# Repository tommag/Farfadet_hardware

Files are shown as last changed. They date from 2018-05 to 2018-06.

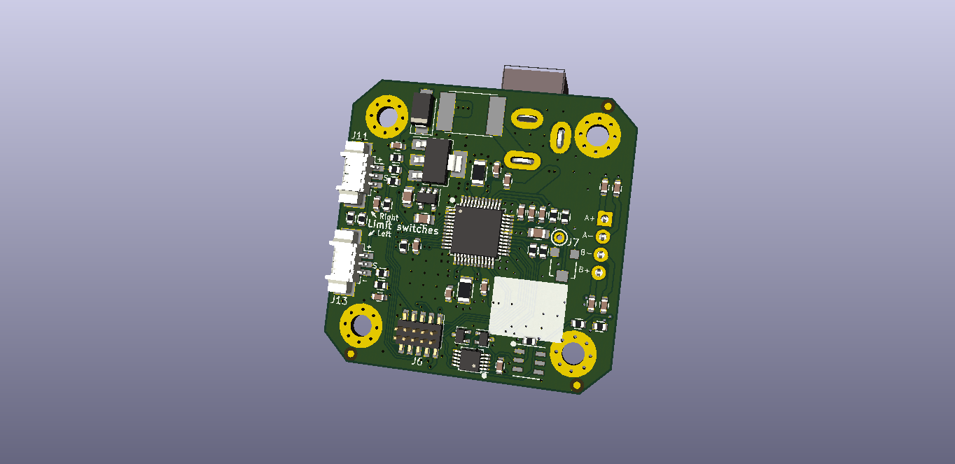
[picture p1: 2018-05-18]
Farfadet_stepper_driver_TMC5130/production/Farfadet_stepper_driver_TMC5130_3D_back.png

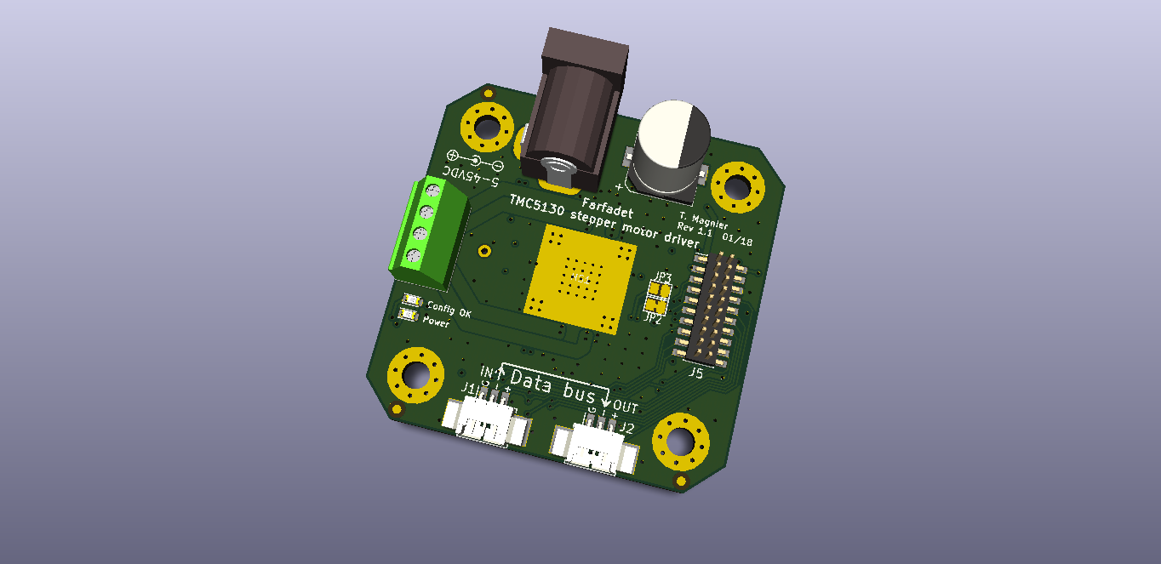
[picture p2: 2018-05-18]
Farfadet_stepper_driver_TMC5130/production/Farfadet_stepper_driver_TMC5130_3D_front.png

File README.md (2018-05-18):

# Farfadet Hardware

This repo contains KiCad EDA files for the Farfadet modular motor system.

You can check some info on the project here : <https://hackaday.io/project/45995-farfadet>

Each folder here contains a different hardware project. There is a schematic export in PDF format for each project. You can find the gerber files in the `gerber` directories. The Bill of Materials and component placement files are in the `production` directories. 

## License
This project is Open Source Hardware, licensed under the Creative Commons BY-SA 4.0 license. You can find the full license text here : <https://creativecommons.org/licenses/by-sa/4.0/>

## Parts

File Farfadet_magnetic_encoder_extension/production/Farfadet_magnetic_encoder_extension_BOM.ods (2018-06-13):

Farfadet – Magnetic encoder extension
Tom Magnier – v1.1 – 06/2018
Reference | Quantity | Value | Package | Digikey part # | Digikey unit price (EUR, qty 10) | Digikey total price
C1,C2 | 2 | 0.1uF | C_0603 | 445-5666-1-ND (https://www.digikey.fr/product-detail/fr/tdk-corporation/CGA3E2X7R1H104K080AA/445-5666-1-ND/2443706) | 0,026 | 0,052
D1 | 1 | Red | LED_0603 | 475-2512-1-ND (https://www.digikey.fr/product-detail/fr/osram-opto-semiconductors-inc/LS-Q976-NR-1/475-2512-1-ND/1802639) | 0,212 | 0,212
D2 | 1 | Green | LED_0603 | 511-1578-1-ND (https://www.digikey.fr/product-detail/fr/rohm-semiconductor/SML-D12M8WT86/511-1578-1-ND/1641810) | 0,21 | 0,21
J1 | 1 | Conn_02x05_Odd_Even | Socket_Strip_Straight_2x05_Pitch1.27mm_SMD | 609-3706-1-ND (https://www.digikey.fr/product-detail/fr/amphenol-fci/20021321-00010C4LF/609-3706-1-ND/2209151) | 0,706 | 0,706
R1 | 1 | 10k | R_0603 | 311-10KGRCT-ND (https://www.digikey.fr/product-detail/fr/yageo/RC0603JR-0710KL/311-10KGRCT-ND/729647) | 0,009 | 0,009
RN1,RN2 | 2 | 4*4.7k | R_Array_Convex_4x0603 | Y9472CT-ND (https://www.digikey.fr/product-detail/fr/panasonic-electronic-components/EXB-38V472JV/Y9472CT-ND/256600) | 0,09 | 0,18
U1 | 1 | AS5132-HSS* | SSOP-20_5.3x7.2mm_Pitch0.65mm | AS5132-HSSMCT-ND (https://www.digikey.fr/product-detail/fr/ams/AS5132-HSSM/AS5132-HSSMCT-ND/3586463) | 5,587 | 5,587
- | 1 | Magnet | NdFeB, Diametrical, diam. 6mm | 469-1024-ND (https://www.digikey.fr/product-detail/fr/radial-magnet-inc/8995/469-1024-ND/5126077) | 0,27 | 0,27
TOTAL |  |  |  |  |  | 7,226
 |  | Adhesive PCB standoff | Height : 6.4mm | RPC1096-ND (https://www.digikey.fr/product-detail/fr/essentra-components/LCBSBM-4-01A-RT/RPC1096-ND/392194) | 0,72

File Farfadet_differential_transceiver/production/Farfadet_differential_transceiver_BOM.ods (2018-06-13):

Farfadet – Differential transceiver for MCU
Tom Magnier – Rev1.0 – 01/2018
Reference | Qty 3.3V | Qty 5V | Value | Package | Digikey part # | Digikey unit price (EUR, qty 10) | Digikey total price | Farnell part # | Farnell unit price
C2 | 1 | 1 | 0.1uF | C_0603 | 445-5666-1-ND (https://www.digikey.fr/product-detail/fr/tdk-corporation/CGA3E2X7R1H104K080AA/445-5666-1-ND/2443706) | 0,026 | 0,026
C1,C3 |  | 2 | 0.1uF | C_0603 | 445-5666-1-ND (https://www.digikey.fr/product-detail/fr/tdk-corporation/CGA3E2X7R1H104K080AA/445-5666-1-ND/2443706) | 0,026 | 0,052
J1,J2 | 2 | 2 | Conn_01x05 | Pin_Header_Straight_1x05_Pitch2.54mm |  |  | 0
J3 | 1 | 1 | XLR connector | Neutrik_XLR_NC3FAAH2 |  |  | 0 | 1310023 (http://fr.farnell.com/neutrik/nc3faah2/socket-xlr-pcb-horizontal-3pole/dp/1310023?st=nc3faa) | 1,15
J4 | 1 | 1 | picoBlade connector | Molex_PicoBlade_53047-0310_03x1.25mm_Straight | WM1732-ND (https://www.digikey.fr/product-detail/fr/molex-llc/0530470310/WM1732-ND/242854) | 0,35 | 0,35
Q1 |  | 1 | BSS84 | SOT-23 | BSS84-FDICT-ND (https://www.digikey.fr/product-detail/fr/diodes-incorporated/BSS84-7-F/BSS84-FDICT-ND/717844) | 0,23 | 0,23
R1 | 1 | 1 | 1k | R_0603 | 311-1.0KGRCT-ND (https://www.digikey.fr/product-detail/fr/yageo/RC0603JR-071KL/311-1.0KGRCT-ND/729624) | 0,009 | 0,009
R3,R4 |  | 2 | 1k | R_0603 | 311-1.0KGRCT-ND (https://www.digikey.fr/product-detail/fr/yageo/RC0603JR-071KL/311-1.0KGRCT-ND/729624) | 0,009 | 0,018
R2 | 1 | 1 | 120R | R_0603 | 311-120GRCT-ND (https://www.digikey.fr/product-detail/fr/yageo/RC0603JR-07120RL/311-120GRCT-ND/729653) | 0,009 | 0,009
U1 |  | 1 | TXS0101DBV | SOT-23-6 | 296-22863-1-ND (https://www.digikey.fr/product-detail/fr/texas-instruments/TXS0101DBVR/296-22863-1-ND/1740010) | 0,54 | 0,54
U2 | 1 |  | SP3485CN | SOIC-8_3.9x4.9mm_Pitch1.27mm | ISL83485IBZ-ND (https://www.digikey.fr/product-detail/fr/intersil/ISL83485IBZ/ISL83485IBZ-ND/821562) | 1,109 | 1,109
U2 |  | 1 | ST485CDR | SOIC-8_3.9x4.9mm_Pitch1.27mm | 497-3734-1-ND (https://www.digikey.fr/product-detail/fr/stmicroelectronics/ST485CDR/497-3734-1-ND/686452) | 0,623 | 0,623
TOTAL |  |  |  |  |  |  | 2,966
 |  |  |  | picoBlade right angle | WM1743-ND (https://www.digikey.fr/product-detail/fr/molex-llc/0530480310/WM1743-ND/242865) | 0,38

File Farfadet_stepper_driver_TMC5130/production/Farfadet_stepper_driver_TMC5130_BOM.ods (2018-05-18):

Farfadet – TMC5130 stepper motor driver
Tom Magnier – Rev1.1 – 01/2018
Reference | Quantity | Value | Package | Digikey part # | Digikey unit price (EUR, qty 10) | Digikey total price
C1 | 1 | 220uF, 50V | CP_Elec_8x10.5 | PCE5025CT-ND (https://www.digikey.fr/product-detail/fr/panasonic-electronic-components/EEE-FT1H221AP/PCE5025CT-ND/2652080) | 0,593 | 0,593
C17,C22 | 2 | DNP | C_0603
C18,C19,C20,C21 | 4 | 470pF, 100V | C_0603 | 490-4949-1-ND (https://www.digikey.fr/product-detail/fr/murata-electronics-north-america/GCM1885C2A471JA16D/490-4949-1-ND/1765268) | 0,064 | 0,256
C2,C4,C5,C10,C15,C16 | 6 | 0.1uF, 16V | C_0603 | 445-5666-1-ND (https://www.digikey.fr/product-detail/fr/tdk-corporation/CGA3E2X7R1H104K080AA/445-5666-1-ND/2443706) | 0,026 | 0,156
C3,C11,C14 | 3 | 0.1uF, 50V | C_0603 | 445-5666-1-ND (https://www.digikey.fr/product-detail/fr/tdk-corporation/CGA3E2X7R1H104K080AA/445-5666-1-ND/2443706) | 0,026 | 0,078
C6 | 1 | 10uF, 10V | C_0805 | 1276-6456-1-ND (https://www.digikey.fr/product-detail/fr/samsung-electro-mechanics-america-inc/CL21A106KPFNNNG/1276-6456-1-ND/5958084) | 0,068 | 0,068
C7,C8 | 2 | 4.7uF, 10V | C_0805 | 1276-6500-1-ND (https://www.digikey.fr/product-detail/fr/samsung-electro-mechanics-america-inc/CL21F475ZPFNNNG/1276-6500-1-ND/5958128) | 0,06 | 0,12
C9 | 1 | 22nF, 63V | C_0603 | 399-3476-1-ND (https://www.digikey.fr/product-detail/fr/kemet/C0603C223K1RACTU/399-3476-1-ND/754769) | 0,028 | 0,028
D1 | 1 | 2A, 50V | D_SMA | B250A-FDICT-ND (https://www.digikey.fr/product-detail/fr/diodes-incorporated/B250A-13-F/B250A-FDICT-ND/768810) | 0,312 | 0,312
D2,D3 | 2 | D5V0L2B3W | SOT-323_SC-70 | D5V0L2B3W-7DICT-ND (https://www.digikey.fr/product-detail/fr/diodes-incorporated/D5V0L2B3W-7/D5V0L2B3W-7DICT-ND/2918820) | 0,226 | 0,452
D6 | 1 | Green | LED_0603 | 511-1578-1-ND (https://www.digikey.fr/product-detail/fr/rohm-semiconductor/SML-D12M8WT86/511-1578-1-ND/1641810) | 0,21 | 0,21
D7 | 1 | Red | LED_0603 | 475-2512-1-ND (https://www.digikey.fr/product-detail/fr/osram-opto-semiconductors-inc/LS-Q976-NR-1/475-2512-1-ND/1802639) | 0,212 | 0,212
F1 | 1 | 1.1A, 60V | Fuse_SMD2920 | F8134CT-ND (https://www.digikey.fr/product-detail/fr/littelfuse-inc/2920L110-60MR/F8134CT-ND/6234828) | 0,614 | 0,614
HS1 | 1 | Heatsink | Heatsink_Adhesive_10x10mm | AE10837-ND (https://www.digikey.fr/product-detail/fr/assmann-wsw-components/V2017B/AE10837-ND/3511410) | 0,48 | 0,48
J11,J2,J1,J13 | 4 | Conn_01x03 | Molex_PicoBlade_53261-0371_03x1.25mm_Angled | WM7621CT-ND (https://www.digikey.fr/product-detail/fr/molex-llc/0532610371/WM7621CT-ND/699108) | 0,84 | 3,36
J12 | 1 | Conn_01x04 | TerminalBlock_Pheonix_MPT-2.54mm_4pol | ED10563-ND (https://www.digikey.fr/product-detail/fr/on-shore-technology-inc/OSTVN04A150/ED10563-ND/1588864) | 1,17 | 1,17
J3 | 1 | BARREL_JACK | JACK_ALIM | CP-202A-ND (https://www.digikey.fr/product-detail/fr/cui-inc/PJ-202A/CP-202A-ND/252007) | 0,473 | 0,473
J5 | 1 | Conn_02x10_Odd_Even | Pin_Header_Straight_2x10_Pitch1.27mm_SMD |  |  | 0
J6 | 1 | Conn_02x05_Odd_Even | Pin_Header_Straight_2x05_Pitch1.27mm_SMD | 609-3695-1-ND (https://www.digikey.fr/product-detail/fr/amphenol-fci/20021121-00010C4LF/609-3695-1-ND/2209147) | 0,588 | 0,588
R11,R17 | 2 | DNP | R_0603 |  |  | 0
R12,R14 | 2 | 4.7k | R_0603 | 311-4.7KGRCT-ND (https://www.digikey.fr/product-detail/fr/yageo/RC0603JR-074K7L/311-4.7KGRCT-ND/729732) | 0,009 | 0,018
R2 | 1 | 10R | R_0603 | 311-10GRCT-ND (https://www.digikey.fr/product-detail/fr/yageo/RC0603JR-0710RL/311-10GRCT-ND/729646) | 0,009 | 0,009
R3 | 1 | 2.2k | R_0603 | 311-2.2KGRCT-ND (https://www.digikey.fr/product-detail/fr/yageo/RC0603JR-072K2L/311-2.2KGRCT-ND/729676) | 0,009 | 0,009
R4,R5 | 2 | 0R12 0.5W | R_1206 | 311-.12LYCT-ND (https://www.digikey.fr/product-detail/fr/yageo/RL1206FR-7W0R12L/311-.12LYCT-ND/3886125) | 0,285 | 0,57
R6,R1,R9,R15,R7,R18 | 6 | 10k | R_0603 | 311-10KGRCT-ND (https://www.digikey.fr/product-detail/fr/yageo/RC0603JR-0710KL/311-10KGRCT-ND/729647) | 0,009 | 0,054
R8,R10,R13,R16 | 4 | 0R | R_0603 | 311-0.0GRCT-ND (https://www.digikey.fr/product-detail/fr/yageo/RC0603JR-070RL/311-0.0GRCT-ND/729622) | 0,008 | 0,032
RV1 | 1 | 10k | Potentiometer_Trimmer-EVM3E | TC33X-103ECT-ND (https://www.digikey.fr/product-detail/fr/bourns-inc/TC33X-2-103E/TC33X-103ECT-ND/612911) | 0,235 | 0,235
U1 | 1 | TS3A24159DGSR | TSSOP-10_3x3mm_Pitch0.5mm | 296-21913-1-ND (https://www.digikey.fr/product-detail/fr/texas-instruments/TS3A24159DGSR/296-21913-1-ND/1629266) | 0,812 | 0,812
U2 | 1 | NCV4264-2ST50 | SOT-223-3Lead_TabPin2 | NCV4264-2ST50T3GOSCT-ND (https://www.digikey.fr/product-detail/fr/on-semiconductor/NCV4264-2ST50T3G/NCV4264-2ST50T3GOSCT-ND/2121724) | 0,879 | 0,879
U3 | 1 | MIC5365-3.3YD5 | SOT-23-5 | 576-4085-1-ND (https://www.digikey.fr/product-detail/fr/microchip-technology/MIC5365-3.3YD5-TR/576-4085-1-ND/3671753) | 0,14 | 0,14
U4 | 1 | DS2431P+T | TSOC-6_4x3.8mm_Pitch1.27mm | DS2431P+T&RCT-ND (https://www.digikey.fr/product-detail/fr/maxim-integrated/DS2431P-T-R/DS2431P-T-RCT-ND/3647900) | 1,383 | 1,383
U5 | 1 | TMC5130A | TQFP-48-1EP_7x7mm_Pitch0.5mm | 1460-1124-ND (https://www.digikey.fr/product-detail/fr/trinamic-motion-control-gmbh/TMC5130A-TA/1460-1124-ND/5030141) | 4,878 | 4,878
TOTAL |  |  |  |  |  | 18,189

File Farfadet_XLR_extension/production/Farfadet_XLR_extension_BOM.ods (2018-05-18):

Farfadet – XLR extension
Tom Magnier – Rev1.0 – 01/2018
Reference | Quantity | Value | Package | Digikey part # | Digikey unit price (EUR, qty 10) | Digikey total price | Farnell part # | Farnell unit price
C1 | 1 | 0.1uF, 50V | C_0603 | 445-5666-1-ND (https://www.digikey.fr/product-detail/fr/tdk-corporation/CGA3E2X7R1H104K080AA/445-5666-1-ND/2443706) | 0,026 | 0,026
C2 | 1 | 22uF, 25V | CP_Elec_6.3x4.5 | PCE3899CT-ND (https://www.digikey.fr/product-detail/fr/panasonic-electronic-components/EEE-1EA220SP/PCE3899CT-ND/766275) | 0,187 | 0,187
C3 | 1 | 1uF, 50V | C_0805 | 1276-3010-1-ND (https://www.digikey.fr/product-detail/fr/samsung-electro-mechanics/CL21F105ZBFNNNE/1276-3010-1-ND/3891096) | 0,069 | 0,069
J1 | 1 | XLR NC3MAAH | Neutrik_XLR_NC3MAAH |  |  | 0 | 1310044 (http://fr.farnell.com/neutrik/nc3maah/plug-xlr-pcb-horizontal-3pole/dp/1310044?st=nc3maa) | 1,08
J2 | 1 | Conn_02x10_Odd_Even | Socket_Strip_Straight_2x10_Pitch1.27mm_SMD | 609-3709-1-ND (https://www.digikey.fr/product-detail/fr/amphenol-fci/20021321-00020C4LF/609-3709-1-ND/2209161) | 1,357 | 1,357
J3 | 1 | XLR NC3FAAH2 | Neutrik_XLR_NC3FAAH2 |  |  | 0 | 1310023 (http://fr.farnell.com/neutrik/nc3faah2/socket-xlr-pcb-horizontal-3pole/dp/1310023?st=nc3faa) | 1,15
J4 | 1 | Conn_01x02 | TerminalBlock_Pheonix_MPT-2.54mm_2pol |  |  | 0
J5 | 1 | Conn_01x02 | JST_PH_B2B-PH-K_02x2.00mm_Straight | 455-1704-ND (https://www.digikey.fr/product-detail/fr/jst-sales-america-inc/B2B-PH-K-S-LF-SN/455-1704-ND/926611) | 0,14 | 0,14
R1 | 1 | 2.2k | R_0603 | 311-2.2KGRCT-ND (https://www.digikey.fr/product-detail/fr/yageo/RC0603JR-072K2L/311-2.2KGRCT-ND/729676) | 0,009 | 0,009
RV1 | 1 | 10k | Potentiometer_Trimmer-EVM3E | TC33X-103ECT-ND (https://www.digikey.fr/product-detail/fr/bourns-inc/TC33X-2-103E/TC33X-103ECT-ND/612911) | 0,235 | 0,235
U1 | 1 | NCV4276BDTADJRKG | TO-252-4 | NCV4276BDTADJRKGOSCT-ND (https://www.digikey.fr/product-detail/fr/on-semiconductor/NCV4276BDTADJRKG/NCV4276BDTADJRKGOSCT-ND/3487445) | 1,231 | 1,231
TOTAL |  |  |  |  |  | 3,254

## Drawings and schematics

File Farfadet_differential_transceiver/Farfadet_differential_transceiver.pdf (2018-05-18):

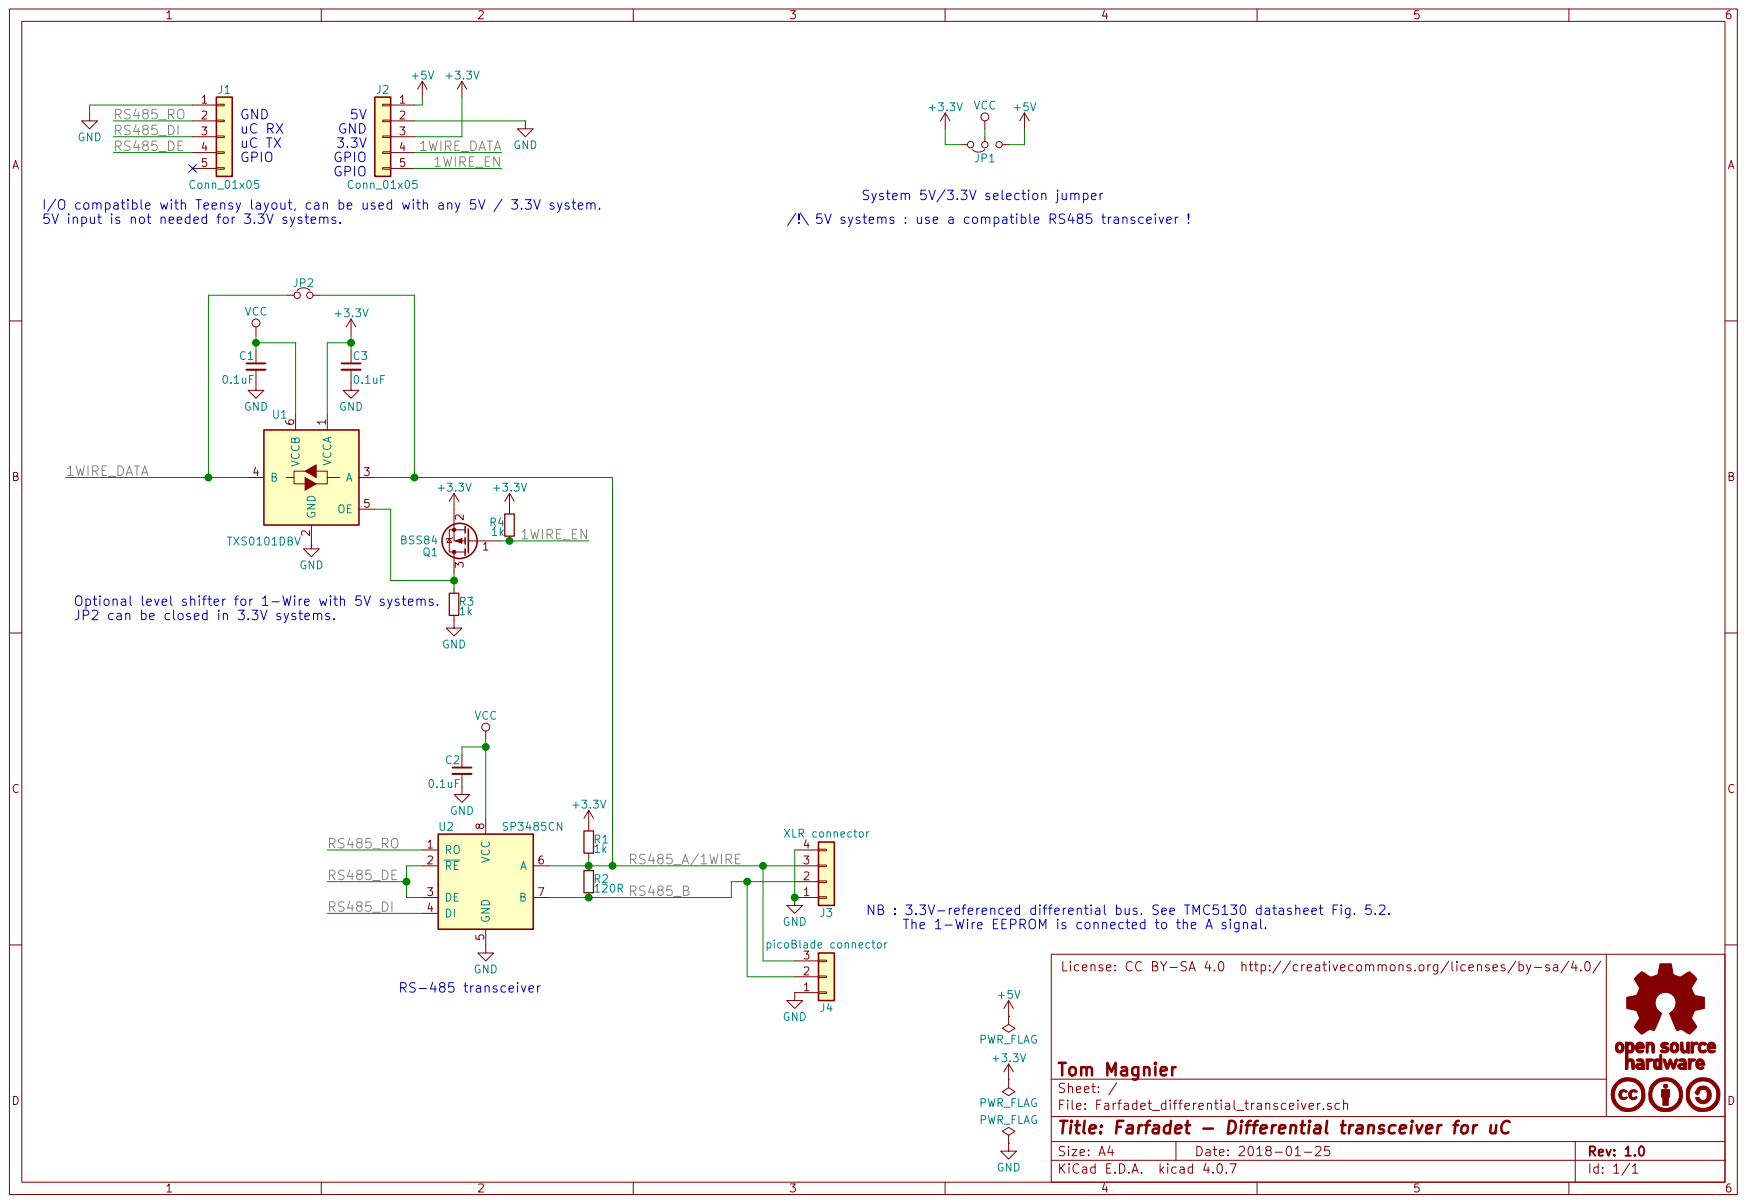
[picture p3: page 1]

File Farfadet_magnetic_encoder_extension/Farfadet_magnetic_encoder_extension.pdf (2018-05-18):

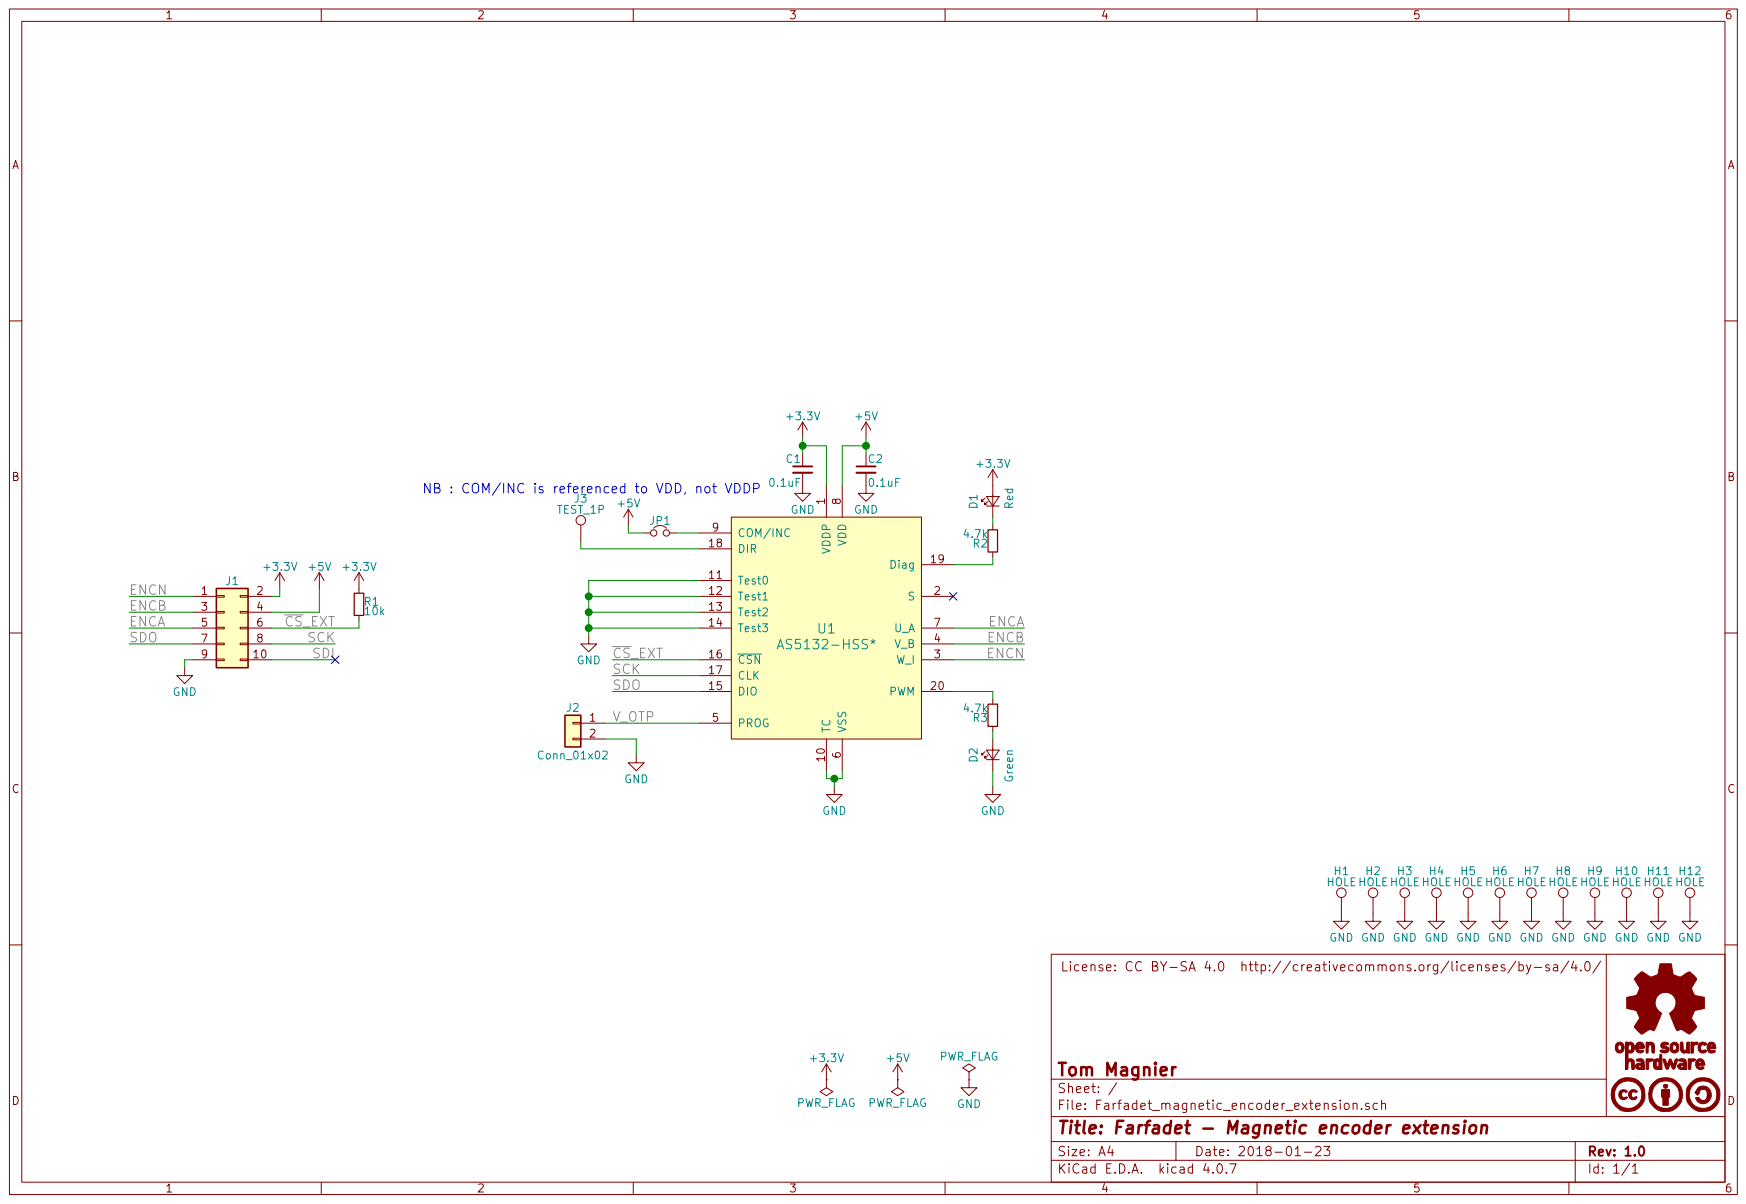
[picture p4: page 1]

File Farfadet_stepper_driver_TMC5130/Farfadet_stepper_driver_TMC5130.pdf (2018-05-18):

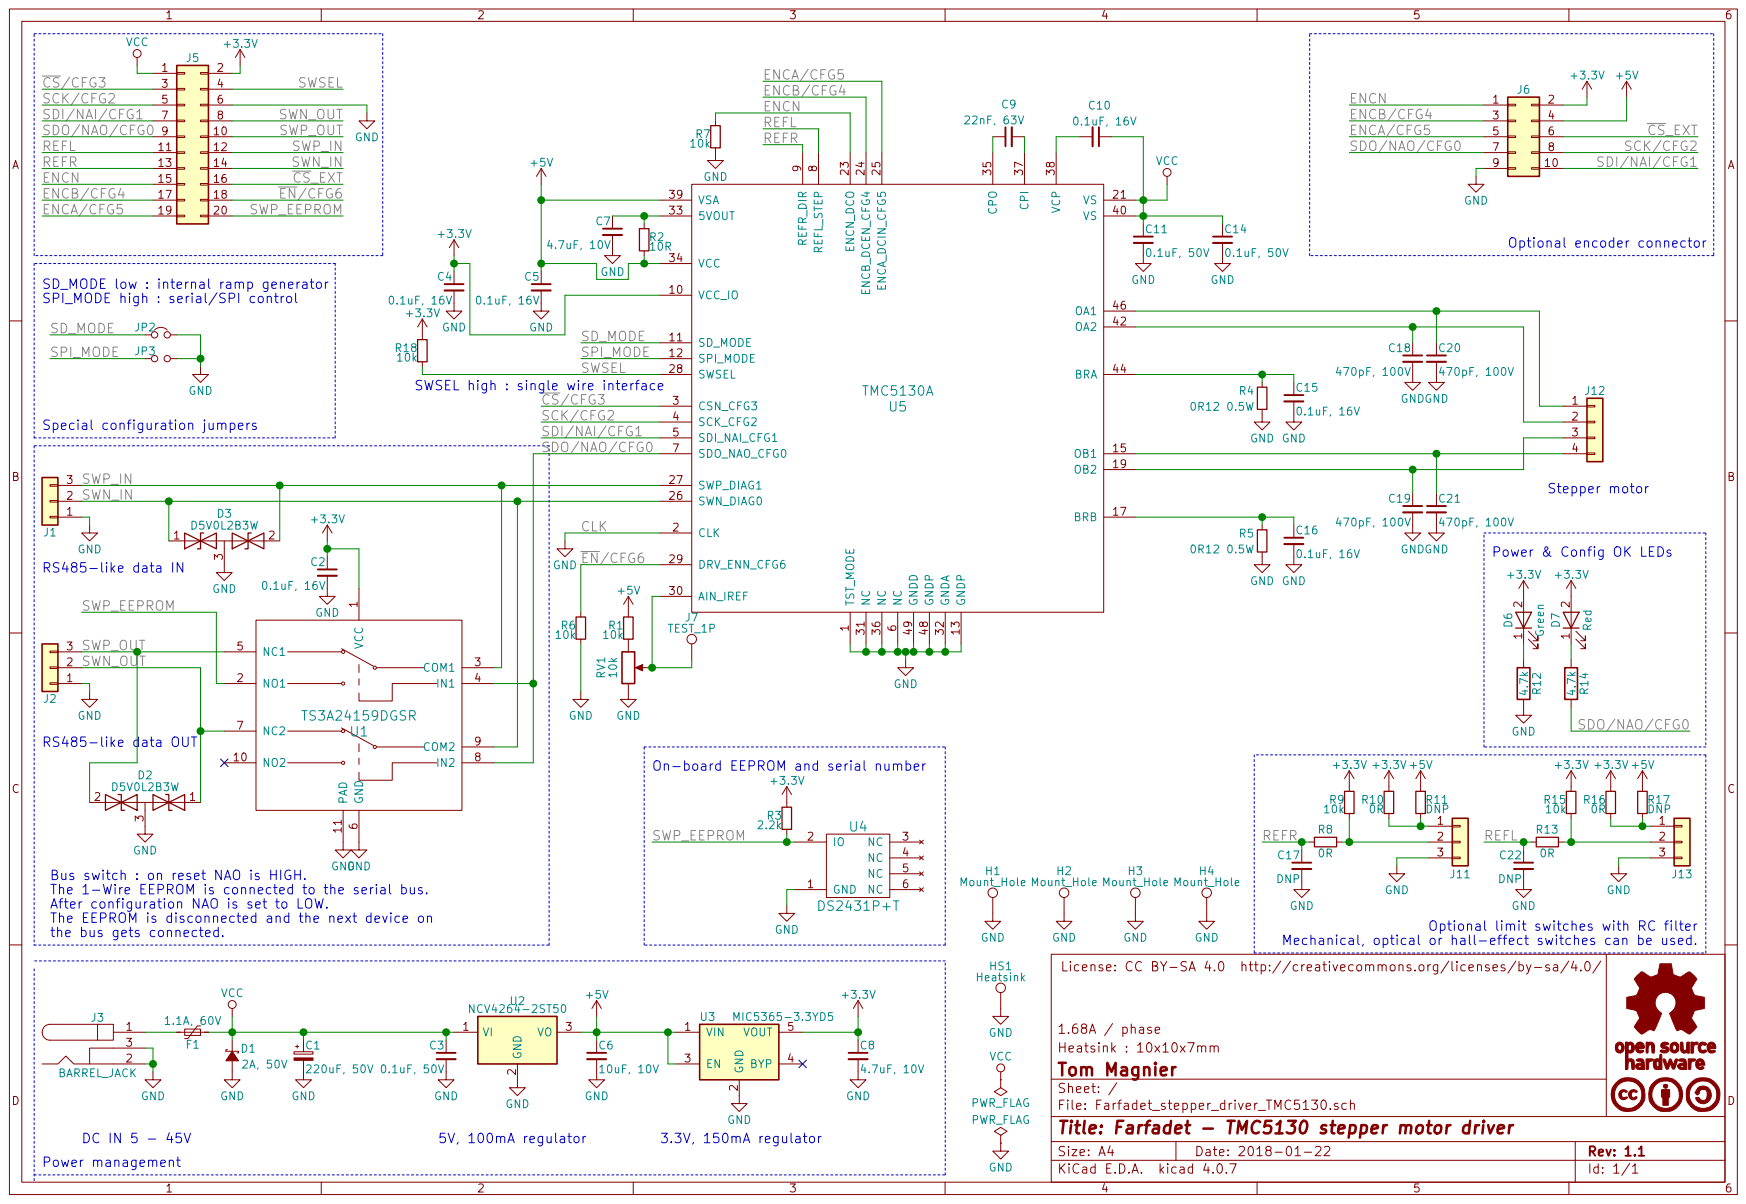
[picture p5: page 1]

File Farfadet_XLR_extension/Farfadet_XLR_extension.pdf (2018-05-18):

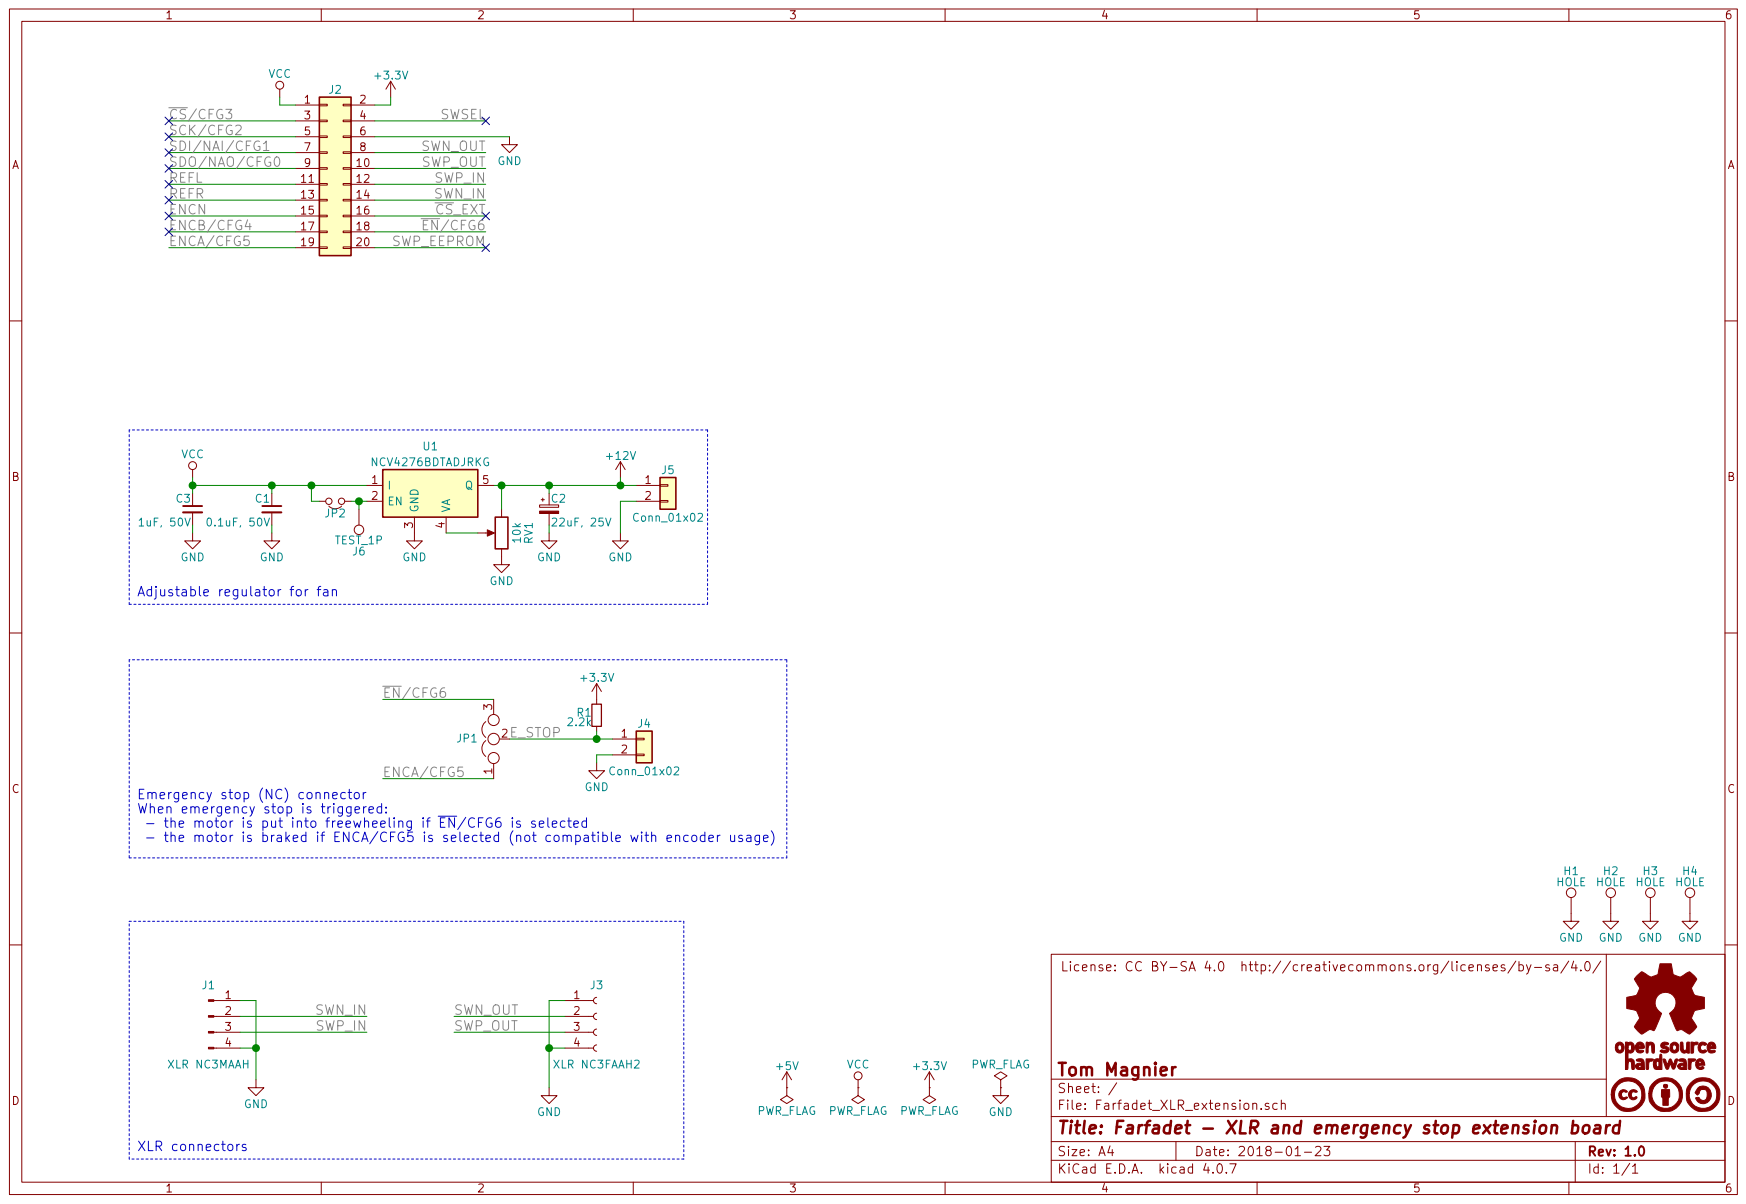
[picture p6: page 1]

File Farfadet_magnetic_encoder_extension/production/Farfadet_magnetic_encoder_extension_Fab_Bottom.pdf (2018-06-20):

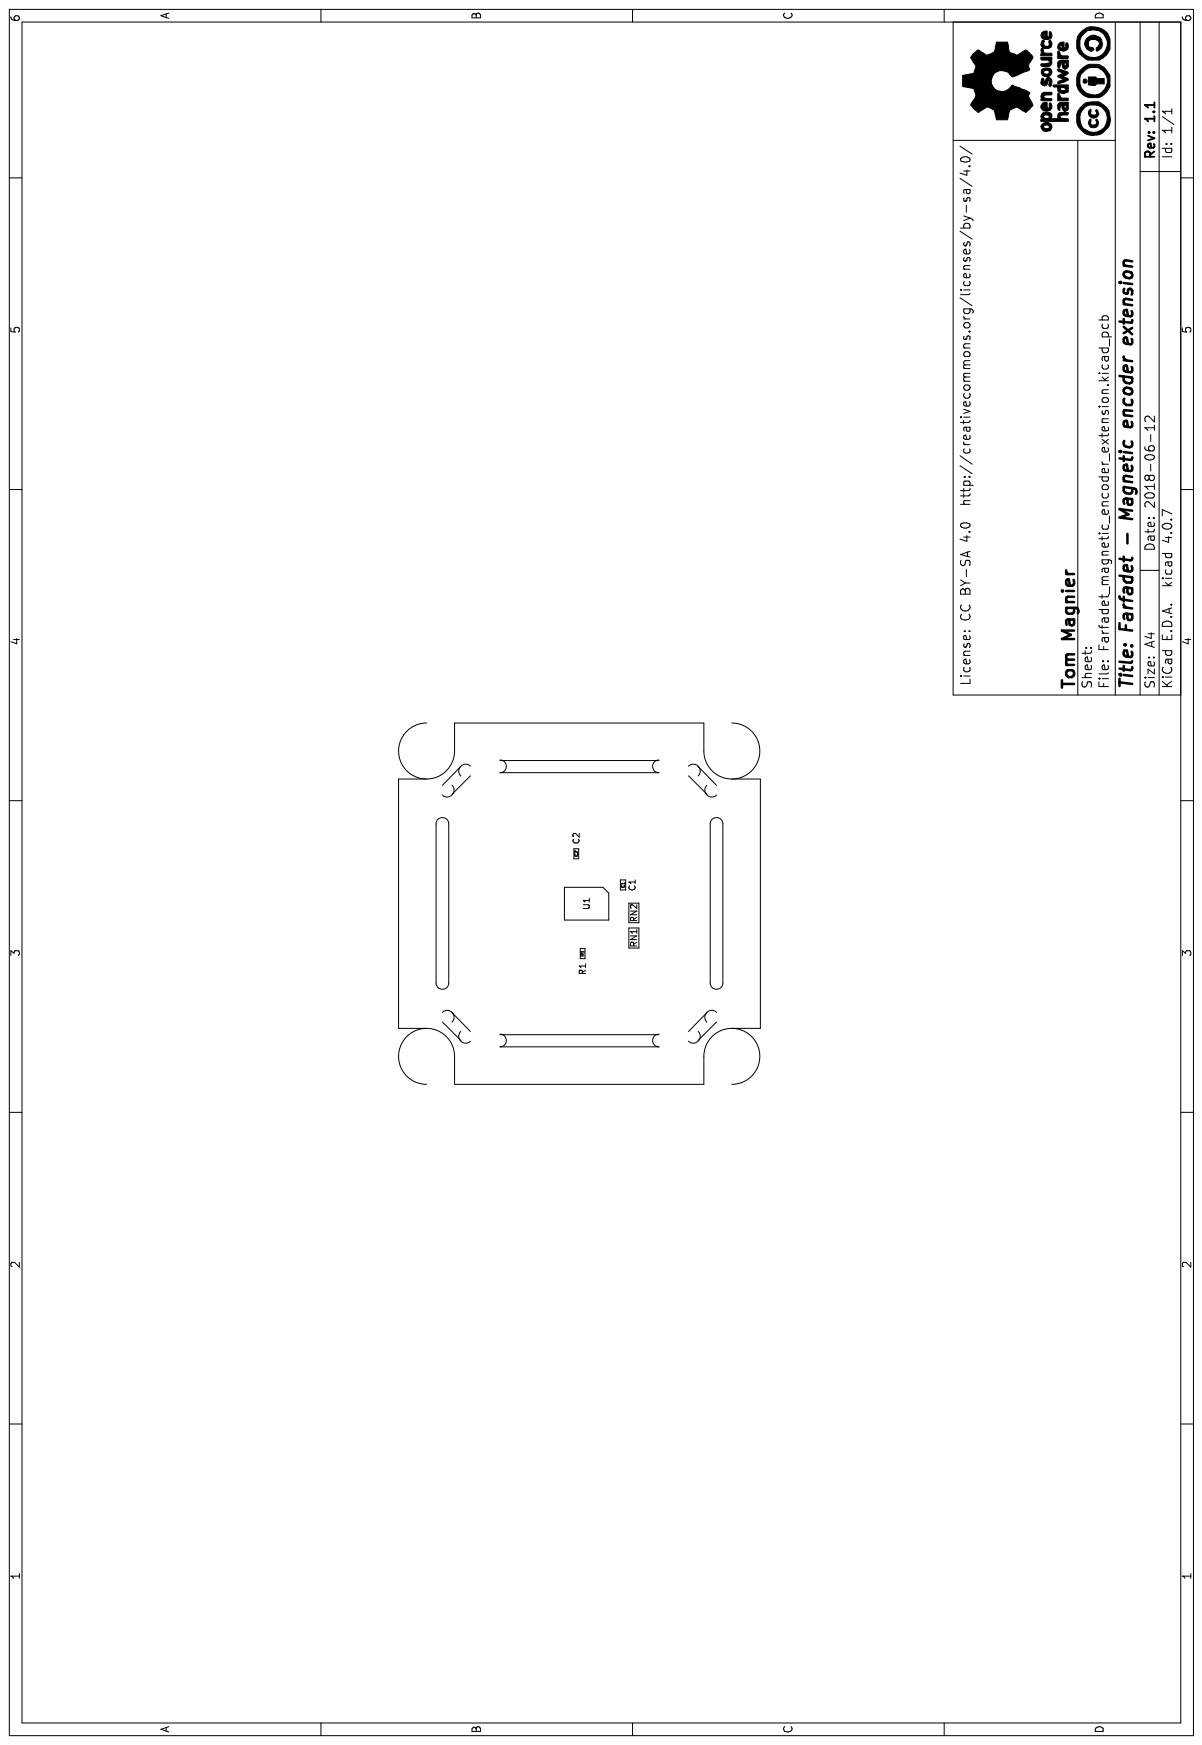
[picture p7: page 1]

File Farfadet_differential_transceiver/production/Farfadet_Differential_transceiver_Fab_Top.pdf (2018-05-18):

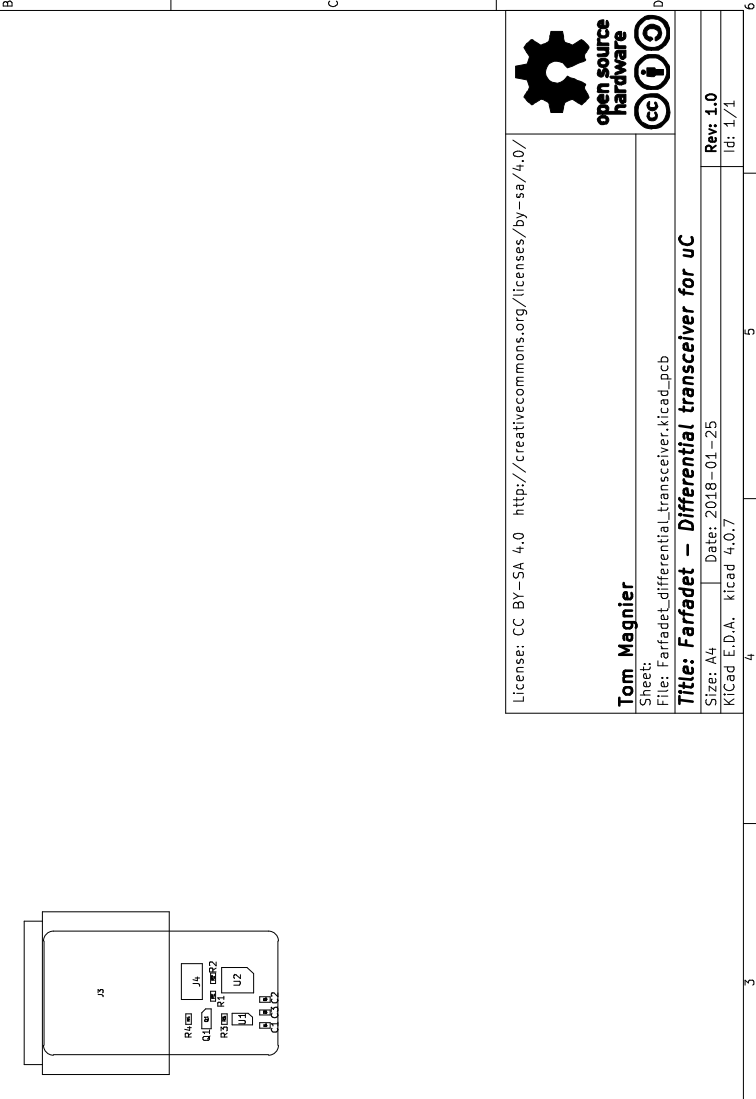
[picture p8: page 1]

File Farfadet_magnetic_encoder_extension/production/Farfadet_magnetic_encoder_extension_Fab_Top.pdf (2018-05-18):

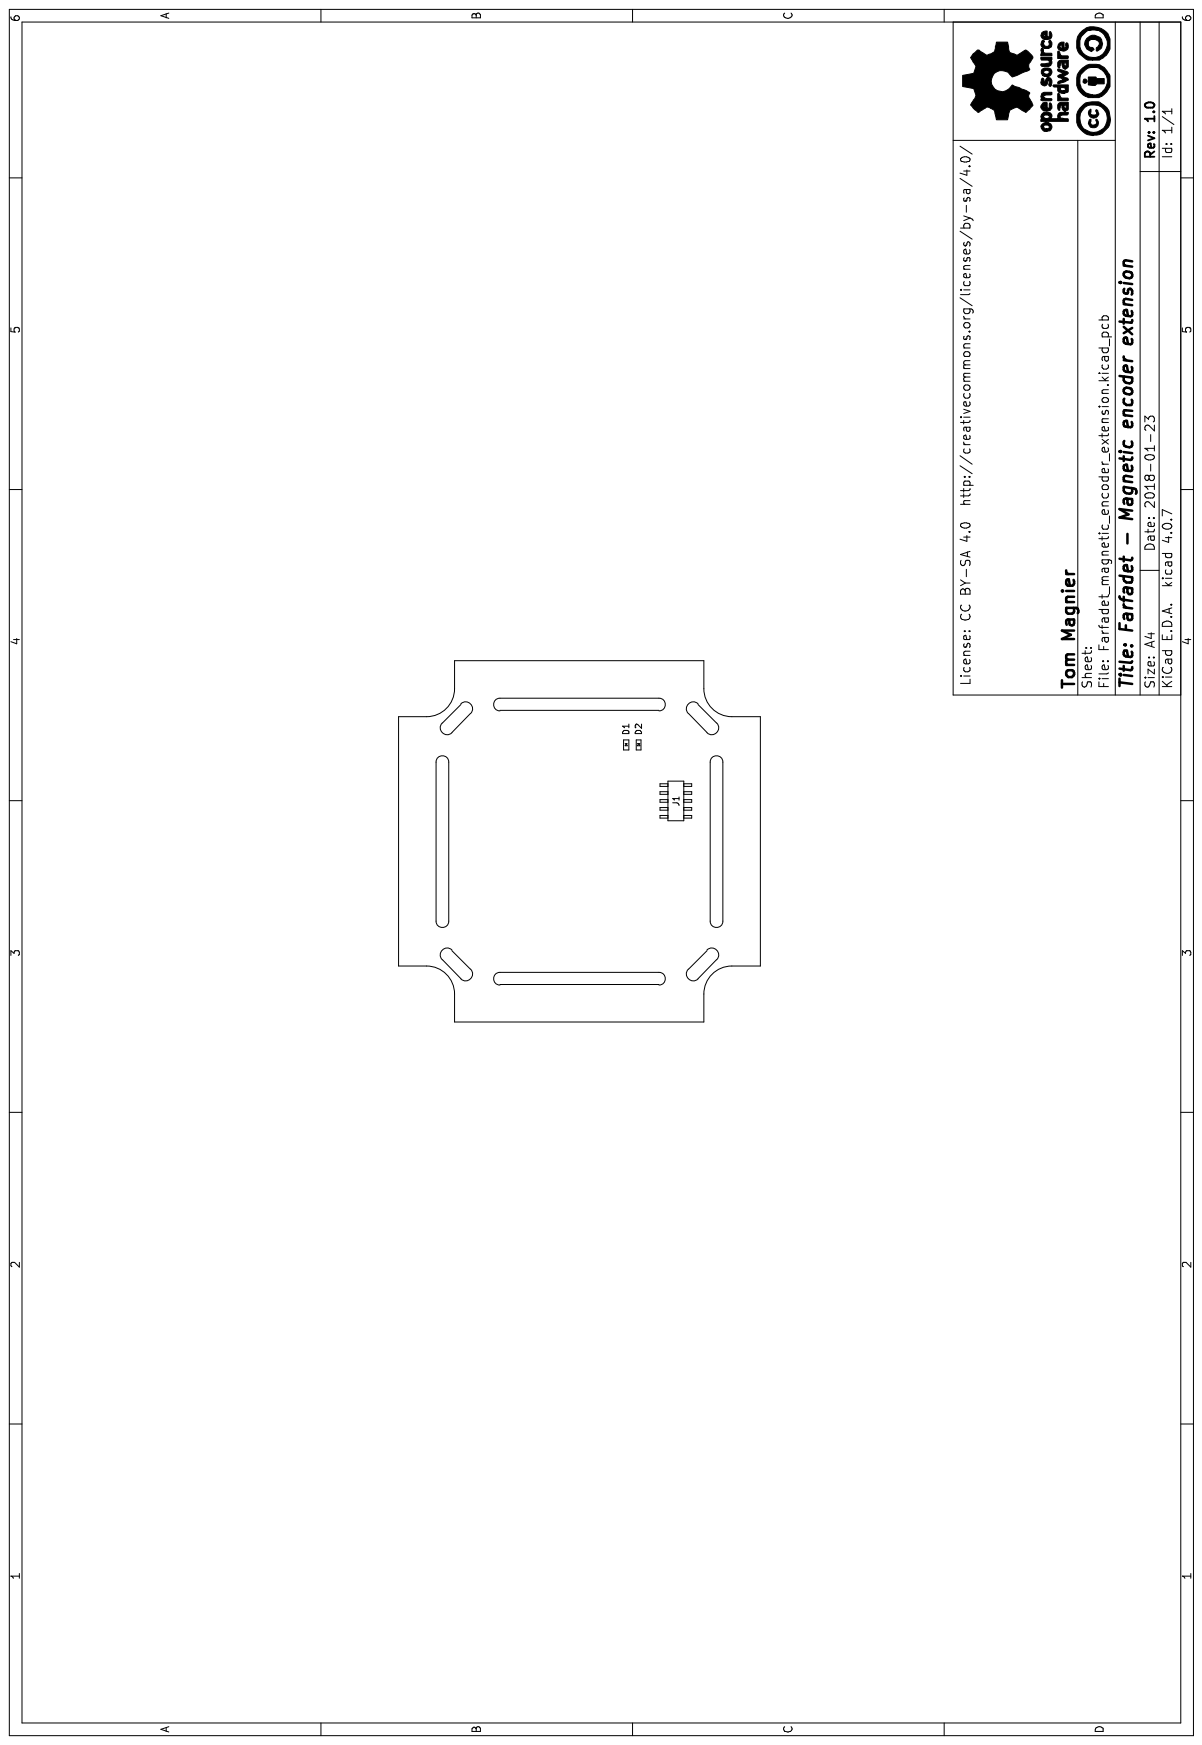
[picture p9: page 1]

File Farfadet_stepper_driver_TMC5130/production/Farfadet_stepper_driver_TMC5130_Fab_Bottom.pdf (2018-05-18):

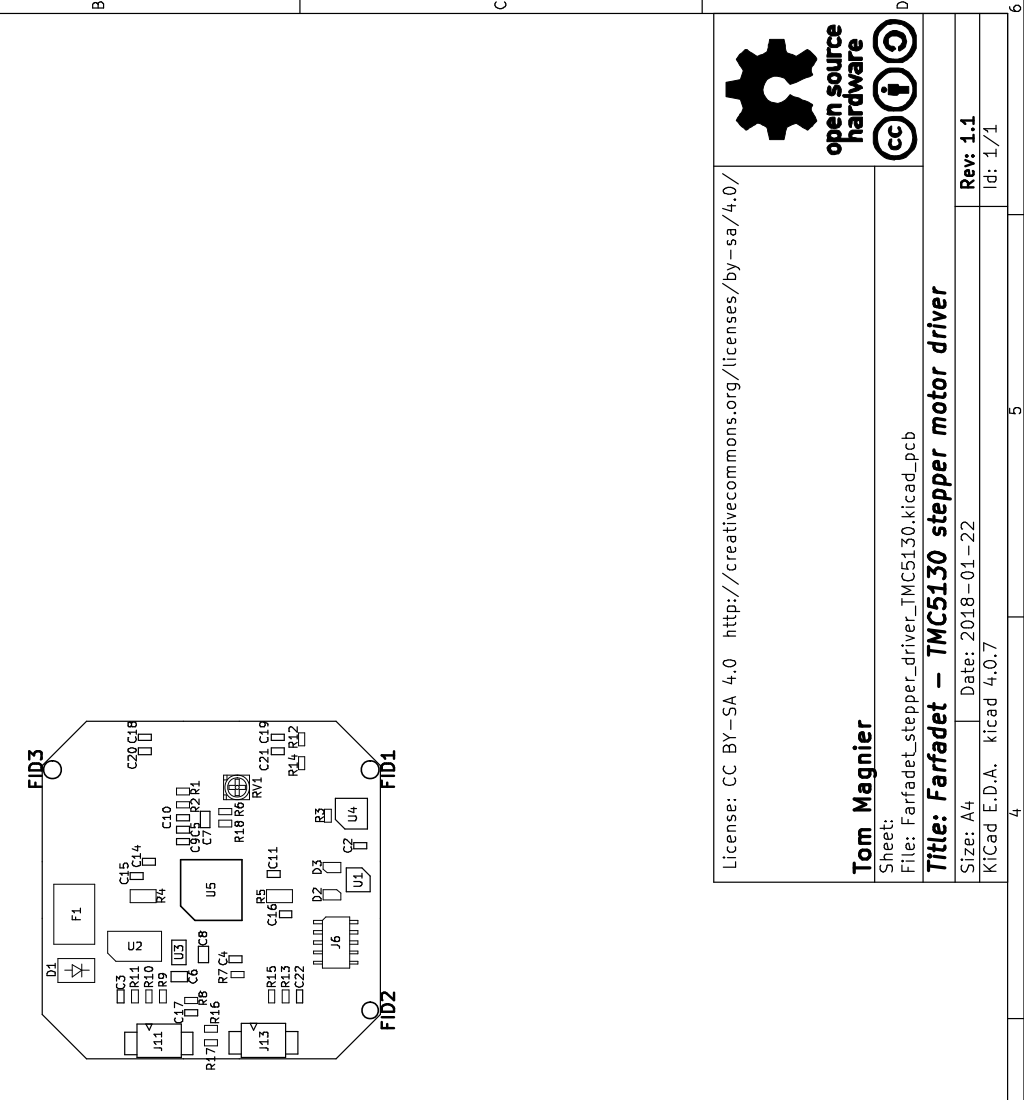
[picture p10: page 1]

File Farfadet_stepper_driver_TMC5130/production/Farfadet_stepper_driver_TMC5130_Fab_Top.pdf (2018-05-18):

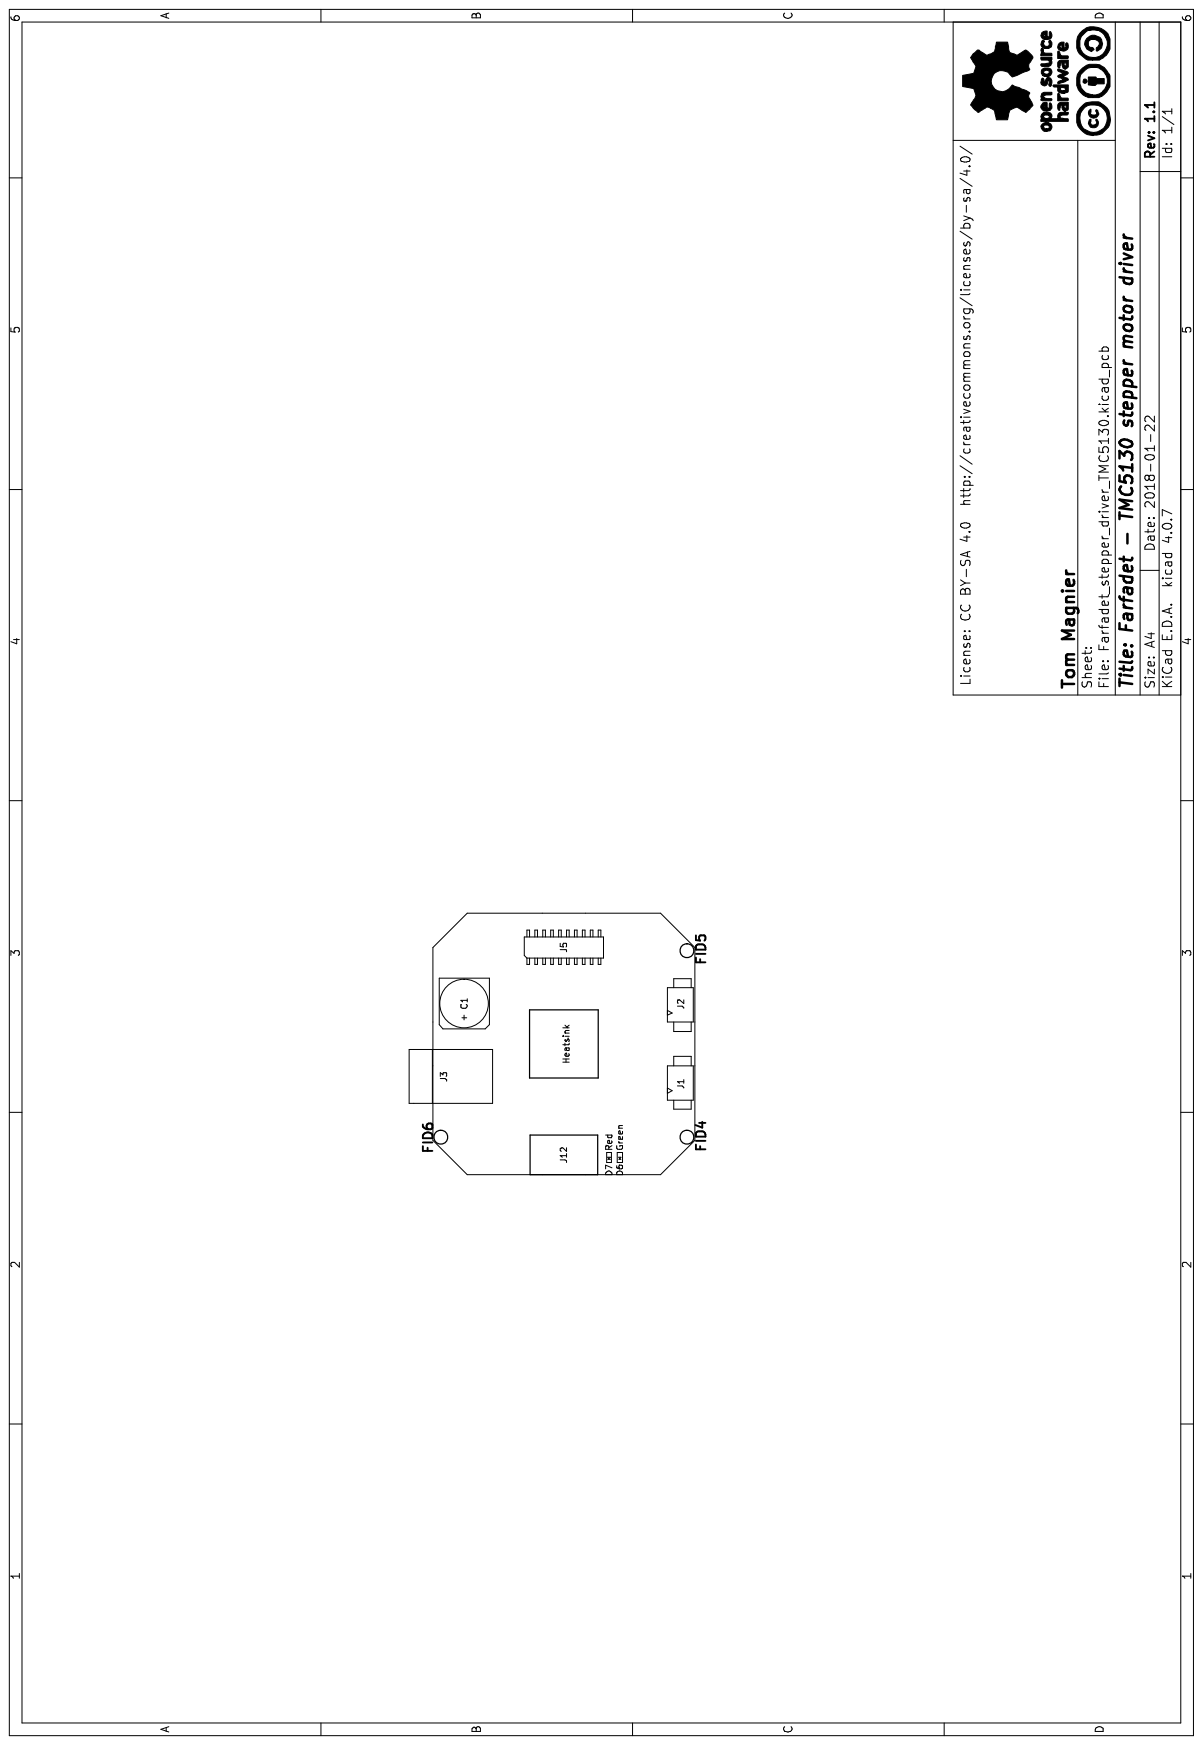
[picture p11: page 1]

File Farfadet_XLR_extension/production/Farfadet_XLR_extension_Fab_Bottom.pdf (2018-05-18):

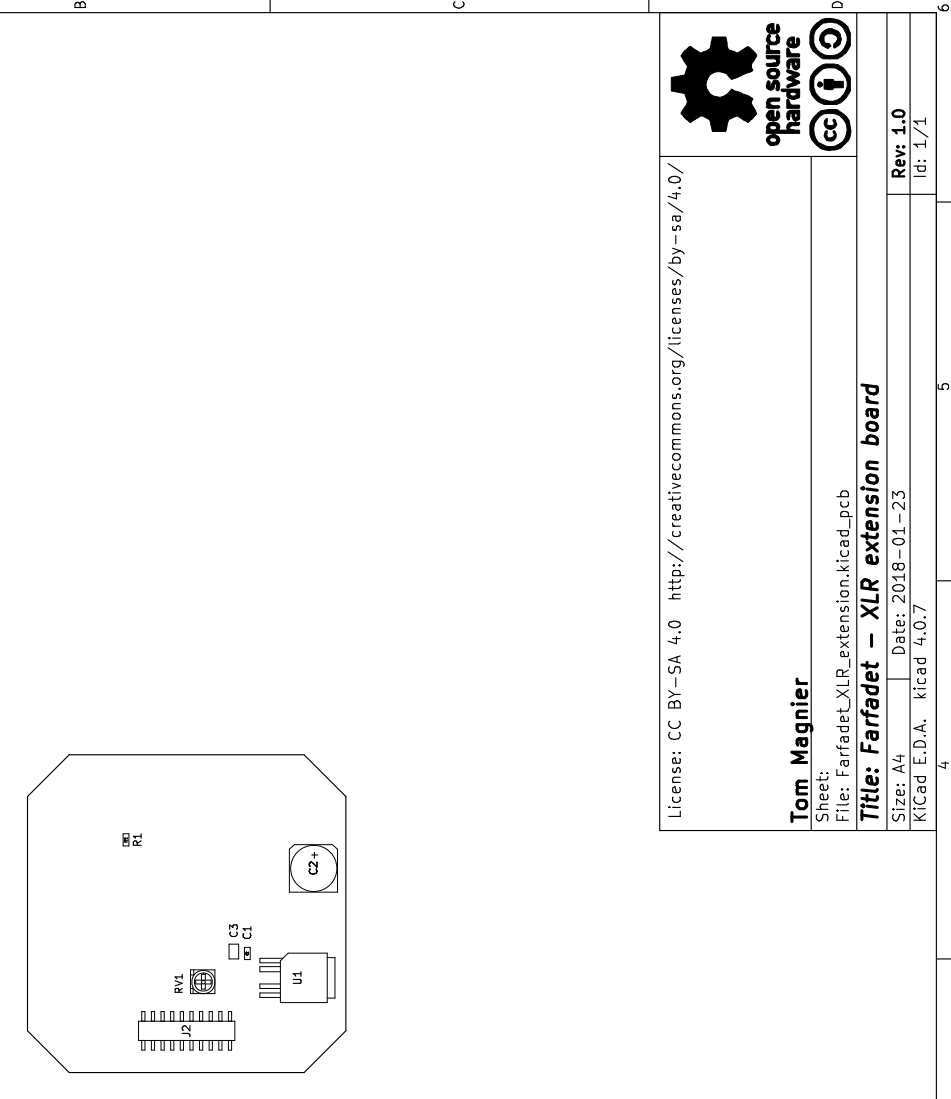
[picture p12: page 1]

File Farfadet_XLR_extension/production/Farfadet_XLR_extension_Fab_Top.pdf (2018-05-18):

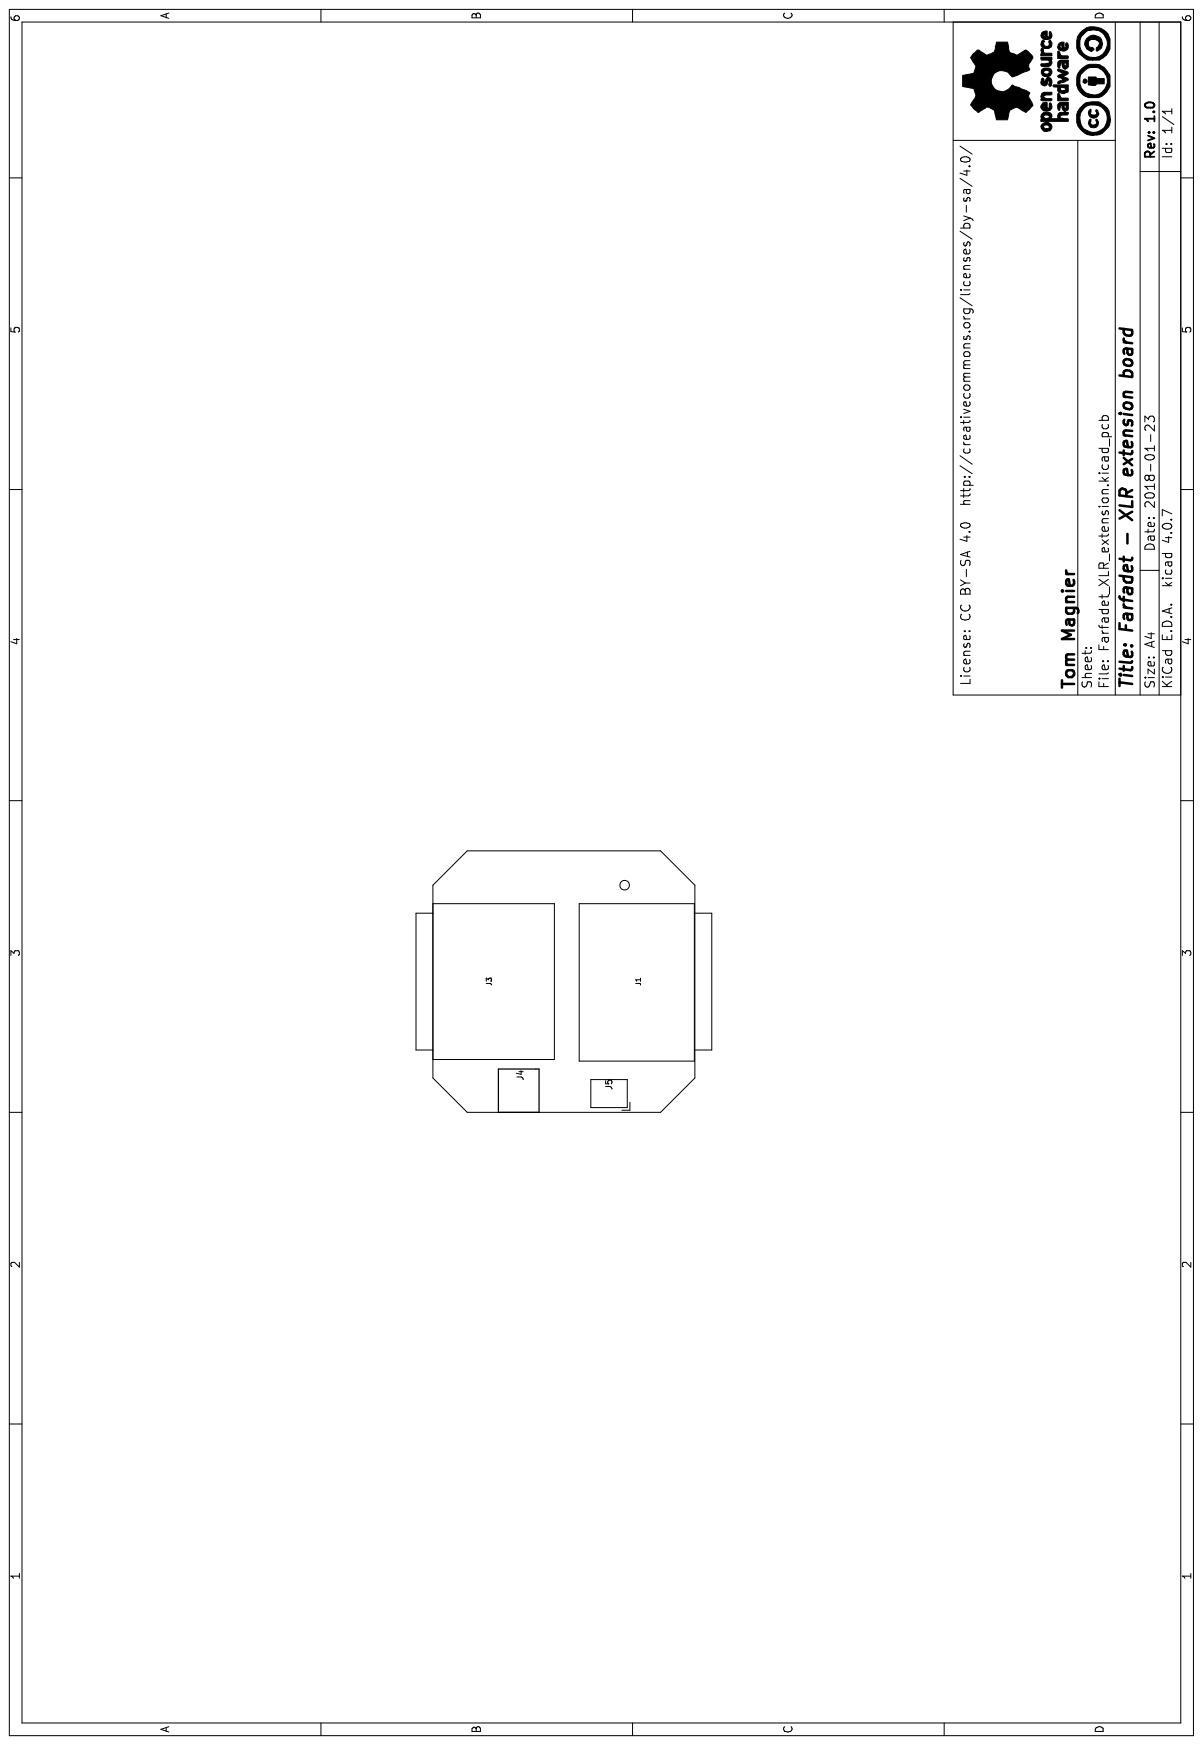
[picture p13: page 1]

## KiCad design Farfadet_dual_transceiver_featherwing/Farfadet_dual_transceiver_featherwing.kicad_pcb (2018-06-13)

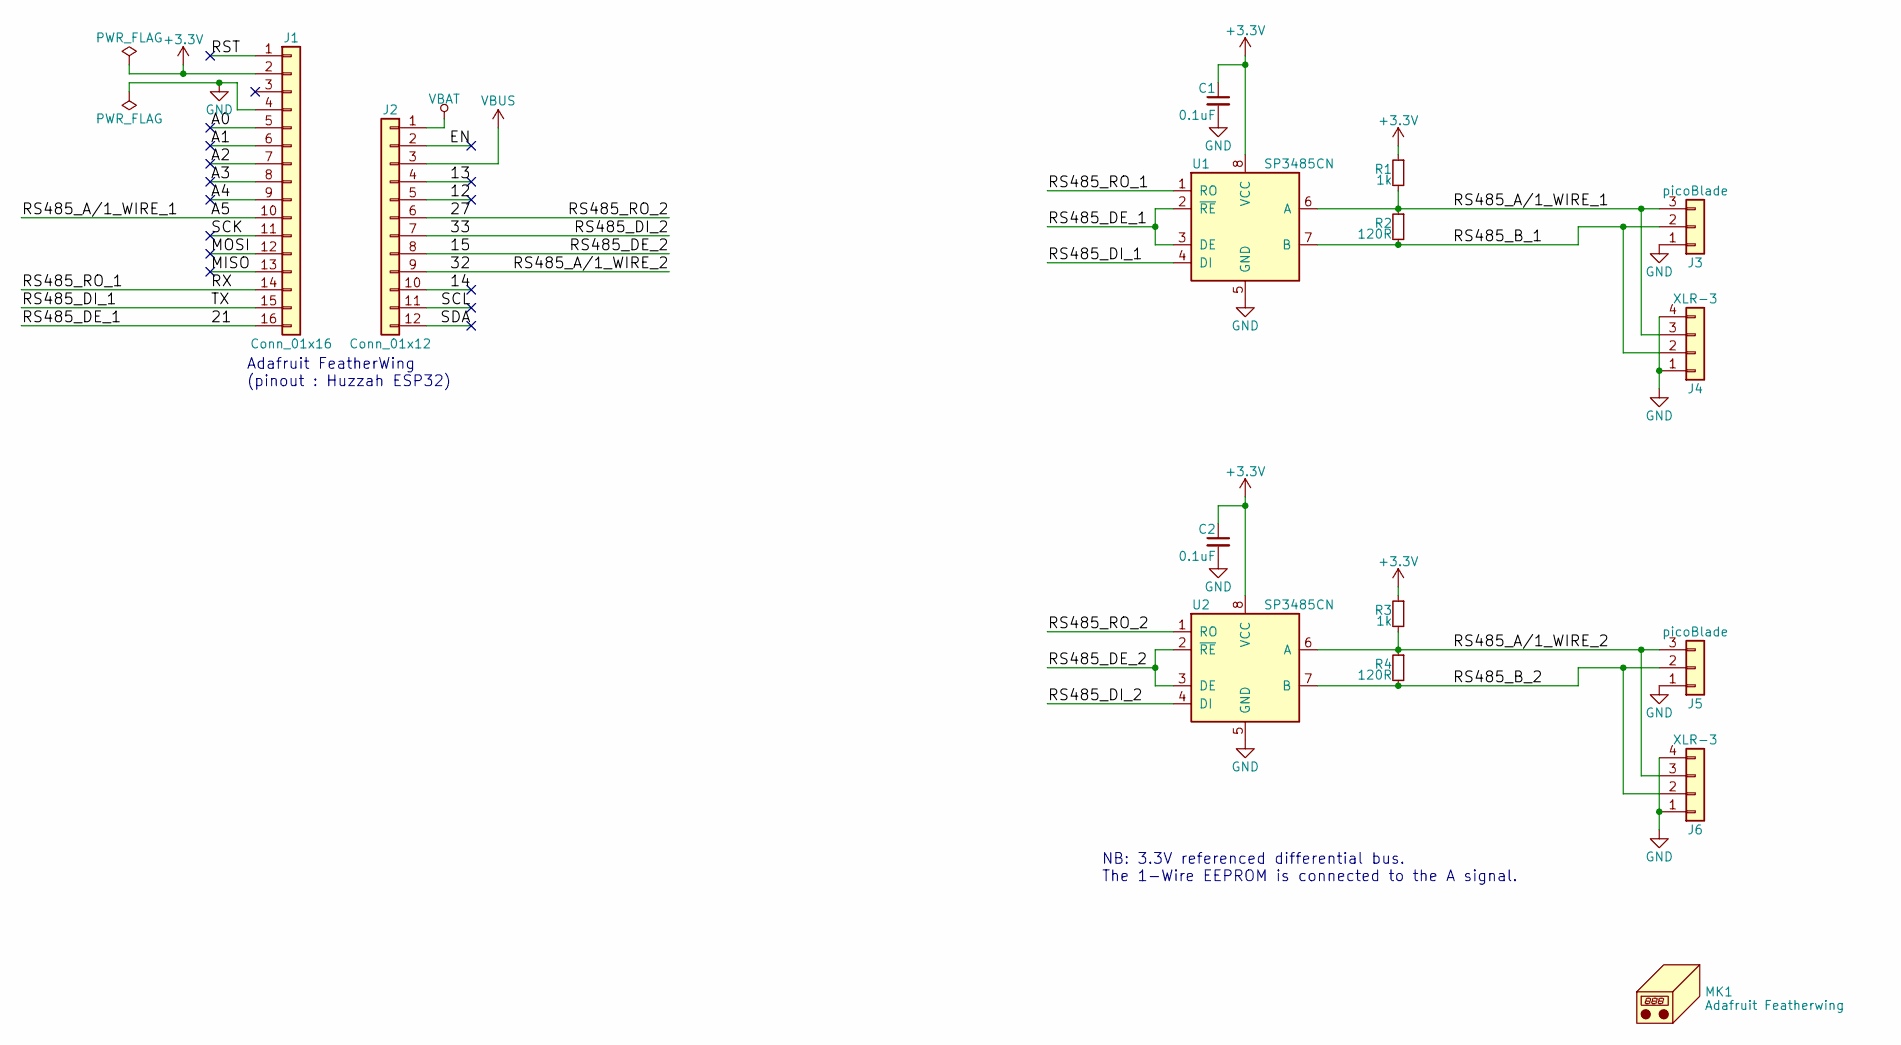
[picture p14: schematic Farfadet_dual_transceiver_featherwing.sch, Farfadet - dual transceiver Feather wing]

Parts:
C1, C2: 0.1uF; C_0603
J1: Conn_01x16; Pin_Header_Straight_1x16_Pitch2.54mm
J2: Conn_01x12; Pin_Header_Straight_1x12_Pitch2.54mm
J3, J5: picoBlade; Molex_PicoBlade_53047-0310_03x1.25mm_Straight
J4, J6: XLR-3; Neutrik_XLR_NC3FAAH2
MK1: Adafruit Featherwing; PCB_FeatherWing
R1, R3: 1k; R_0603
R2, R4: 120R; R_0603
U1, U2: SP3485CN; SOIC-8_3.9x4.9mm_Pitch1.27mm

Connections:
+3V3: C1.1, C2.1, J1.2, R1.1, R3.1, U1.8 (VCC), U2.8 (VCC)
/12: J2.5
/13: J2.4
/14: J2.10
/15: J2.8, U2.2 (~RE~), U2.3 (DE)
/21: J1.16, U1.2 (~RE~), U1.3 (DE)
/27: J2.6, U2.1 (RO)
/32: J2.9, J5.3, J6.3, R3.2, R4.1, U2.6 (A)
/33: J2.7, U2.4 (DI)
/A0: J1.5
/A1: J1.6
/A2: J1.7
/A3: J1.8
/A4: J1.9
/A5: J1.10, J3.3, J4.3, R1.2, R2.1, U1.6 (A)
/EN: J2.2
/MISO: J1.13
/MOSI: J1.12
/RS485_B_1: J3.2, J4.2, R2.2, U1.7 (B)
/RS485_B_2: J5.2, J6.2, R4.2, U2.7 (B)
/RS485_DI_1: J1.15, U1.4 (DI)
/RS485_RO_1: J1.14, U1.1 (RO)
/RST: J1.1
/SCK: J1.11
/SCL: J2.11
/SDA: J2.12
GND: C1.2, C2.2, J1.4, J3.1, J4.1, J4.4, J5.1, J6.1, J6.4, U1.5 (GND), U2.5 (GND)
VBAT: J2.1
VBUS: J2.3

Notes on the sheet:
Adafruit FeatherWing (pinout : Huzzah ESP32)
NB: 3.3V referenced differential bus. The 1-Wire EEPROM is connected to the A signal.

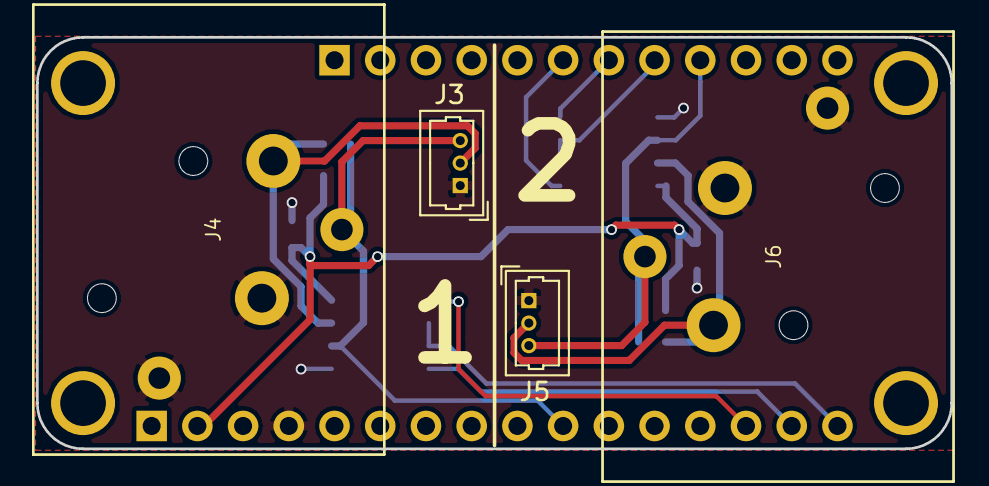
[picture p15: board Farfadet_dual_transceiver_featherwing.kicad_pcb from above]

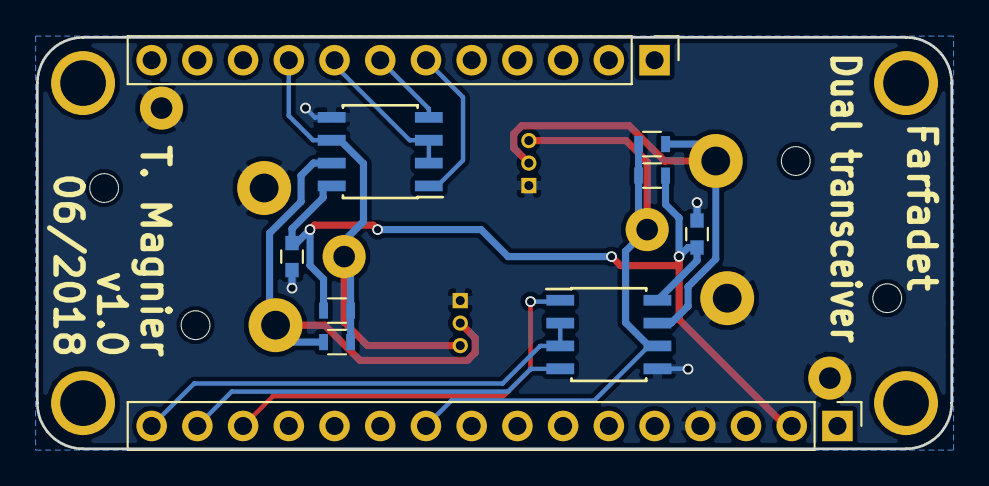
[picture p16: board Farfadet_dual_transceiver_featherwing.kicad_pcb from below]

Board: 2 copper layers, 50.8 x 22.9 mm, 15 parts (10 on the bottom side), 12 nets.

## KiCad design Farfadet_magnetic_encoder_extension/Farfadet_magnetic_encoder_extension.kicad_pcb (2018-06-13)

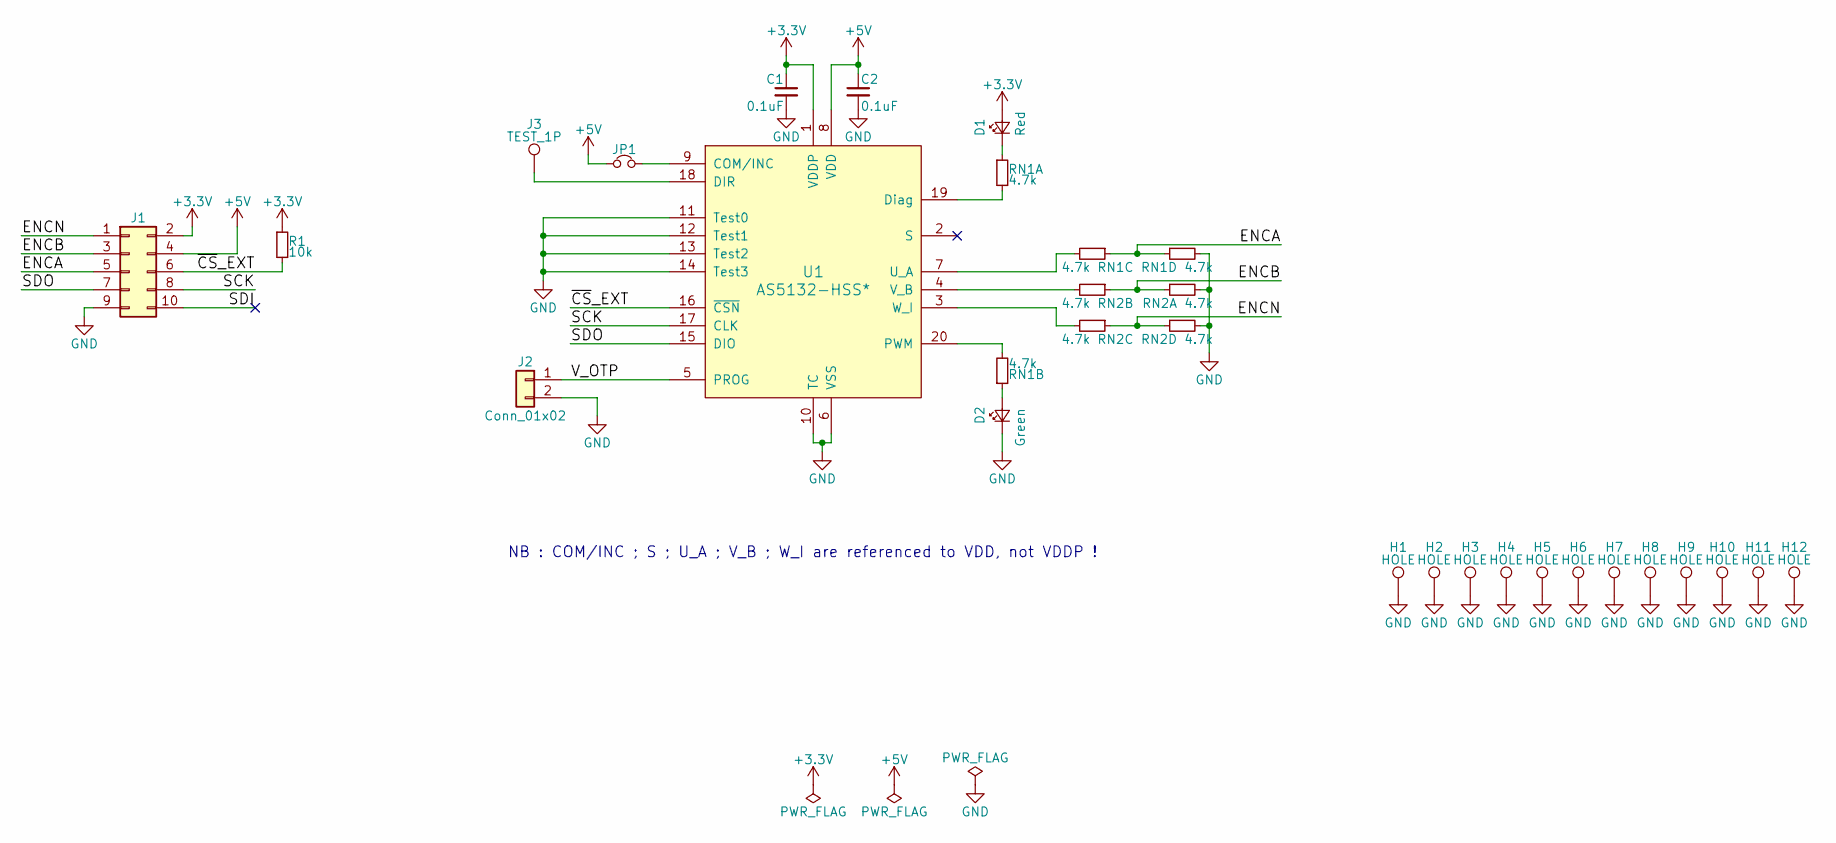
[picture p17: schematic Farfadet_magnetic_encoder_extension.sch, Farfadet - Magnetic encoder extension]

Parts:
C1, C2: 0.1uF; C_0603
D1: Red; LED_0603
D2: Green; LED_0603
H1, H2, H3, H4, H5, H6, H7, H8, H9, H10, H11, H12: HOLE; MountingHole_3.2mm_M3_Pad_Via
J1: Conn_02x05_Odd_Even; Socket_Strip_Straight_2x05_Pitch1.27mm_SMD
J2: Conn_01x02; Test_Point_2Pads
J3: TEST_1P; Measurement_Point_Round-TH_Small
JP1: Jumper_NC_Small; Solder_Jumper_2_conn
R1: 10k; R_0603
RN1, RN2: 4.7k; R_Array_Convex_4x0603
U1: AS5132-HSS*; SSOP-20_5.3x7.2mm_Pitch0.65mm

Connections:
+3V3: C1.1, D1.2 (A), J1.2, R1.1, U1.1 (VDDP)
+5V: C2.1, J1.4, JP1.1, U1.8 (VDD)
/ENCA: J1.5, RN1.3, RN1.4
/ENCB: J1.3, RN2.1, RN2.2
/ENCN: J1.1, RN2.3, RN2.4
/SCK: J1.8, U1.17 (CLK)
/SDI: J1.10
/SDO: J1.7, U1.15 (DIO)
/V_OTP: J2.1, U1.5 (PROG)
/~CS~_EXT: J1.6, R1.2, U1.16 (~CSN)
GND: C1.2, C2.2, D2.1 (K), H1.1, H2.1, H3.1, H4.1, H5.1, H6.1, H7.1, H8.1, H9.1, H10.1, H11.1, H12.1, J1.9, J2.2, RN1.5, RN2.5, RN2.8, U1.6 (VSS), U1.10 (TC), U1.11 (Test0), U1.12 (Test1), U1.13 (Test2), U1.14 (Test3)
unnamed: D1.1 (K), RN1.1
unnamed: D2.2 (A), RN1.2
unnamed: J3.1, U1.18 (DIR)
unnamed: JP1.2, U1.9 (COM/INC)
unnamed: RN1.6, U1.7 (U_A)
unnamed: RN1.7, U1.20 (PWM)
unnamed: RN1.8, U1.19 (Diag)
unnamed: RN2.6, U1.3 (W_I)
unnamed: RN2.7, U1.4 (V_B)

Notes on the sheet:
NB : COM/INC ; S ; U_A ; V_B ; W_I are referenced to VDD, not VDDP !

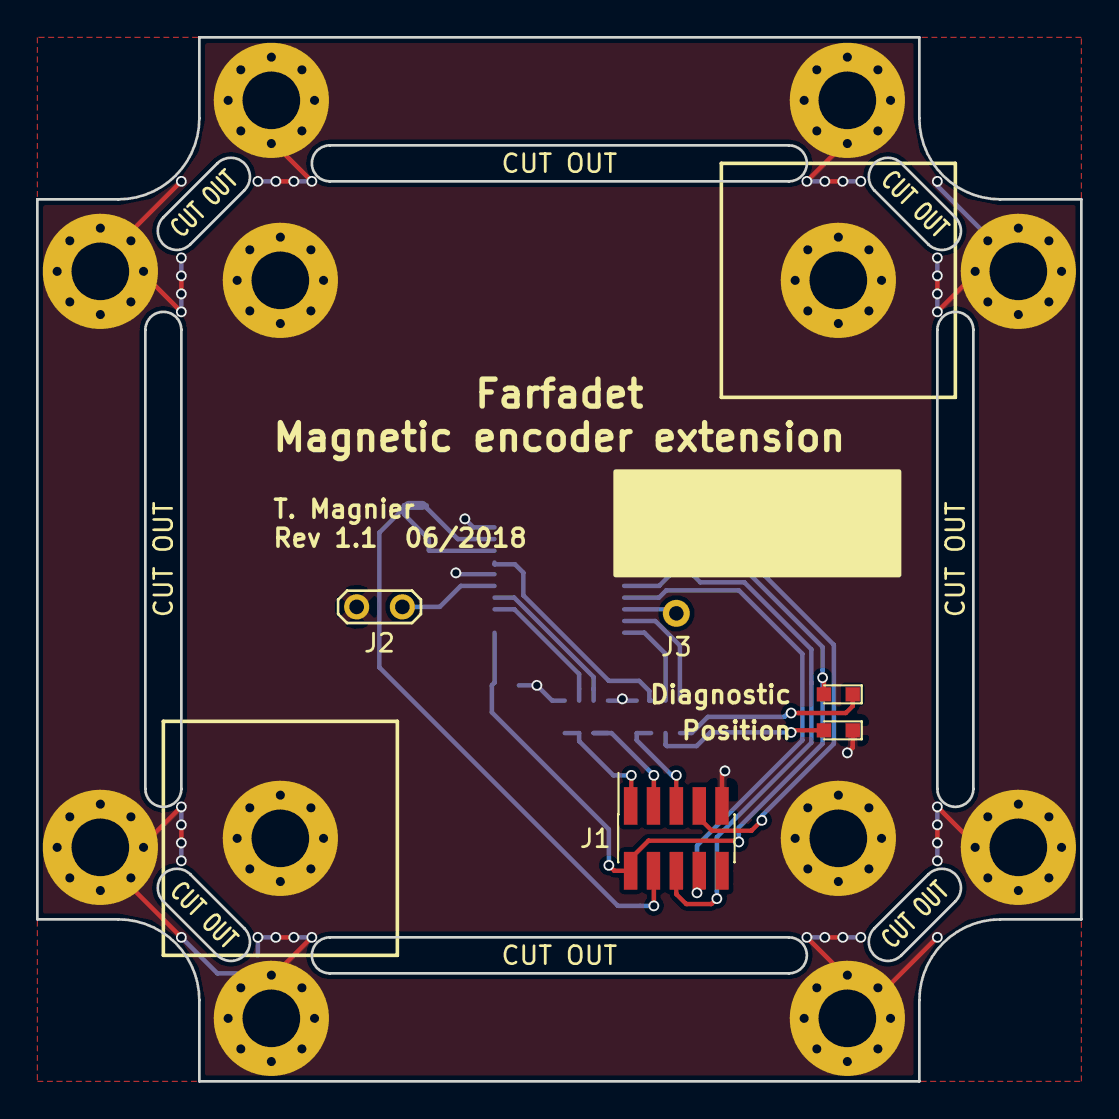
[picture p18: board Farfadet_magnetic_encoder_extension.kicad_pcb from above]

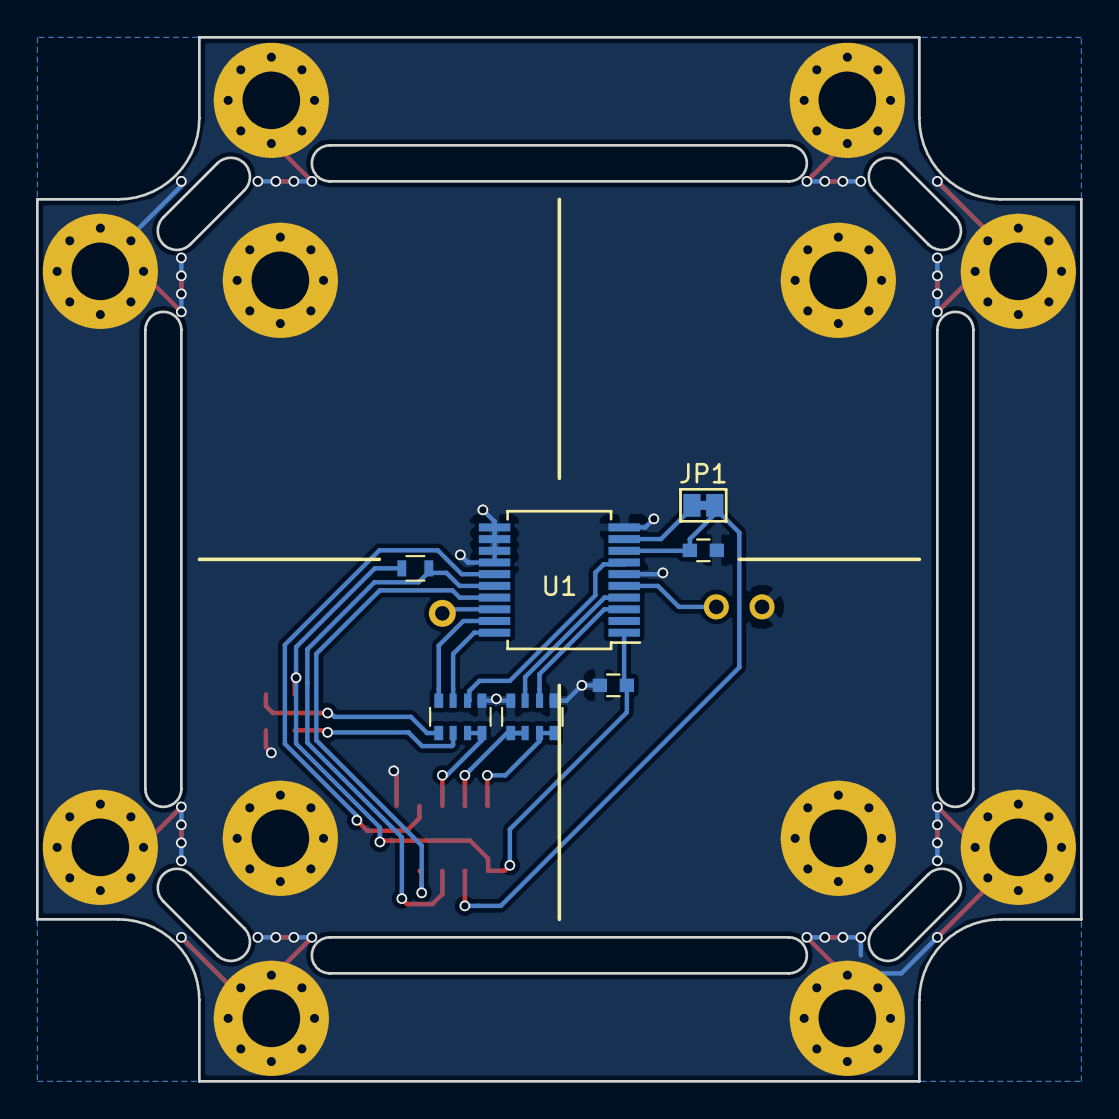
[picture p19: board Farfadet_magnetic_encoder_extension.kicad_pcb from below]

Board: 2 copper layers, 58.0 x 58.0 mm, 24 parts (7 on the bottom side), 19 nets.

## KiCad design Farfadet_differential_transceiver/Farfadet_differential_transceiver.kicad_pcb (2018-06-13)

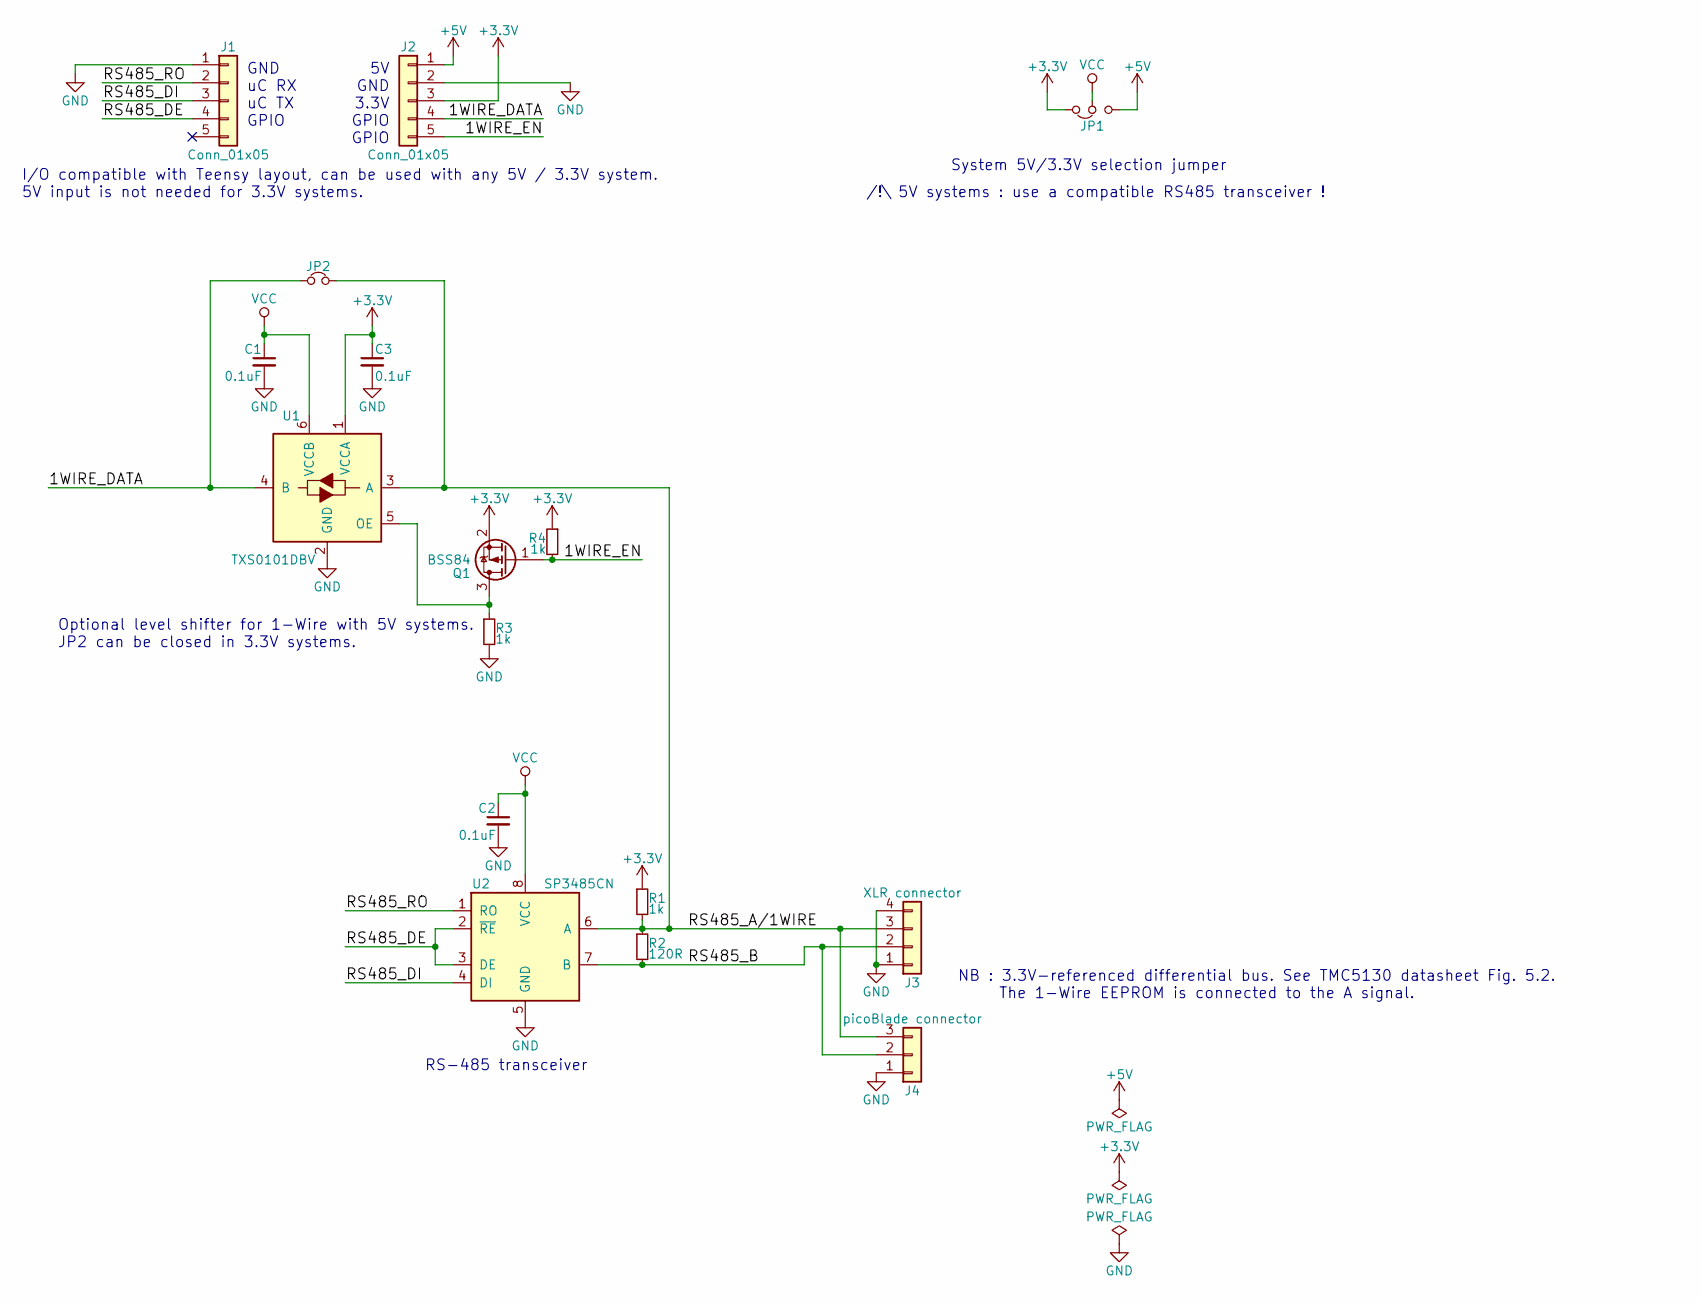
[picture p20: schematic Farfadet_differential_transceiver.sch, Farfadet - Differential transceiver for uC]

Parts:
C1, C2, C3: 0.1uF; C_0603
J1, J2: Conn_01x05; Pin_Header_Straight_1x05_Pitch2.54mm
J3: XLR connector; Neutrik_XLR_NC3FAAH2
J4: picoBlade connector; Molex_PicoBlade_53047-0310_03x1.25mm_Straight
JP1: Jumper_Dual_NC_NO_Small; Solder_Jumper_3_conn_1-2
JP2: Jumper_NC_Small; Solder_Jumper_2_conn
Q1: BSS84; SOT-23
R1, R3, R4: 1k; R_0603
R2: 120R; R_0603
U1: TXS0101DBV; SOT-23-6
U2: SP3485CN; SOIC-8_3.9x4.9mm_Pitch1.27mm

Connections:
+3V3: C3.1, J2.3, JP1.1, Q1.2 (S), R1.1, R4.1, U1.1 (VCCA)
+5V: J2.1, JP1.3
/1WIRE_DATA: J2.4, JP2.1, U1.4 (B)
/1WIRE_EN: J2.5, Q1.1 (G), R4.2
/RS485_A/1WIRE: J3.3, J4.3, JP2.2, R1.2, R2.1, U1.3 (A), U2.6 (A)
/RS485_B: J3.2, J4.2, R2.2, U2.7 (B)
/RS485_DE: J1.4, U2.2 (~RE~), U2.3 (DE)
/RS485_DI: J1.3, U2.4 (DI)
/RS485_RO: J1.2, U2.1 (RO)
GND: C1.2, C2.2, C3.2, J1.1, J2.2, J3.1, J3.4, J4.1, R3.2, U1.2 (GND), U2.5 (GND)
unnamed: Q1.3 (D), R3.1, U1.5 (OE)
VCC: C1.1, C2.1, JP1.2, U1.6 (VCCB), U2.8 (VCC)

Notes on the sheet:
I/O compatible with Teensy layout, can be used with any 5V / 3.3V system. 5V input is not needed for 3.3V systems.
GND uC RX uC TX GPIO
5V GND 3.3V GPIO GPIO
System 5V/3.3V selection jumper
/!\ 5V systems : use a compatible RS485 transceiver !
NB : 3.3V-referenced differential bus. See TMC5130 datasheet Fig. 5.2. The 1-Wire EEPROM is connected to the A signal.
RS-485 transceiver
Optional level shifter for 1-Wire with 5V systems. JP2 can be closed in 3.3V systems.

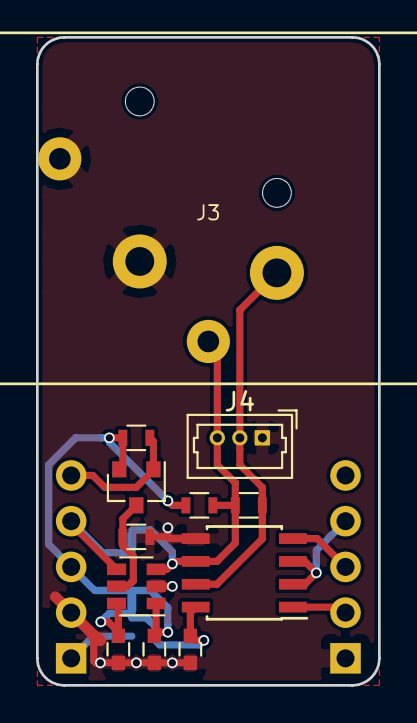
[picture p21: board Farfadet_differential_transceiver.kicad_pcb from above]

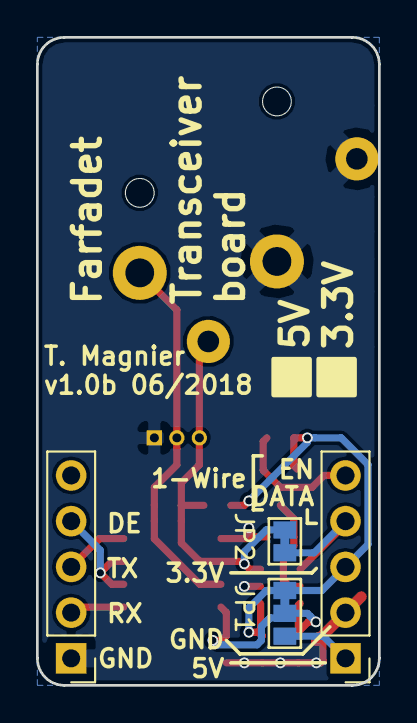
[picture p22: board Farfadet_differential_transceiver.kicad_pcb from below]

Board: 2 copper layers, 19.0 x 36.0 mm, 16 parts (4 on the bottom side), 12 nets.

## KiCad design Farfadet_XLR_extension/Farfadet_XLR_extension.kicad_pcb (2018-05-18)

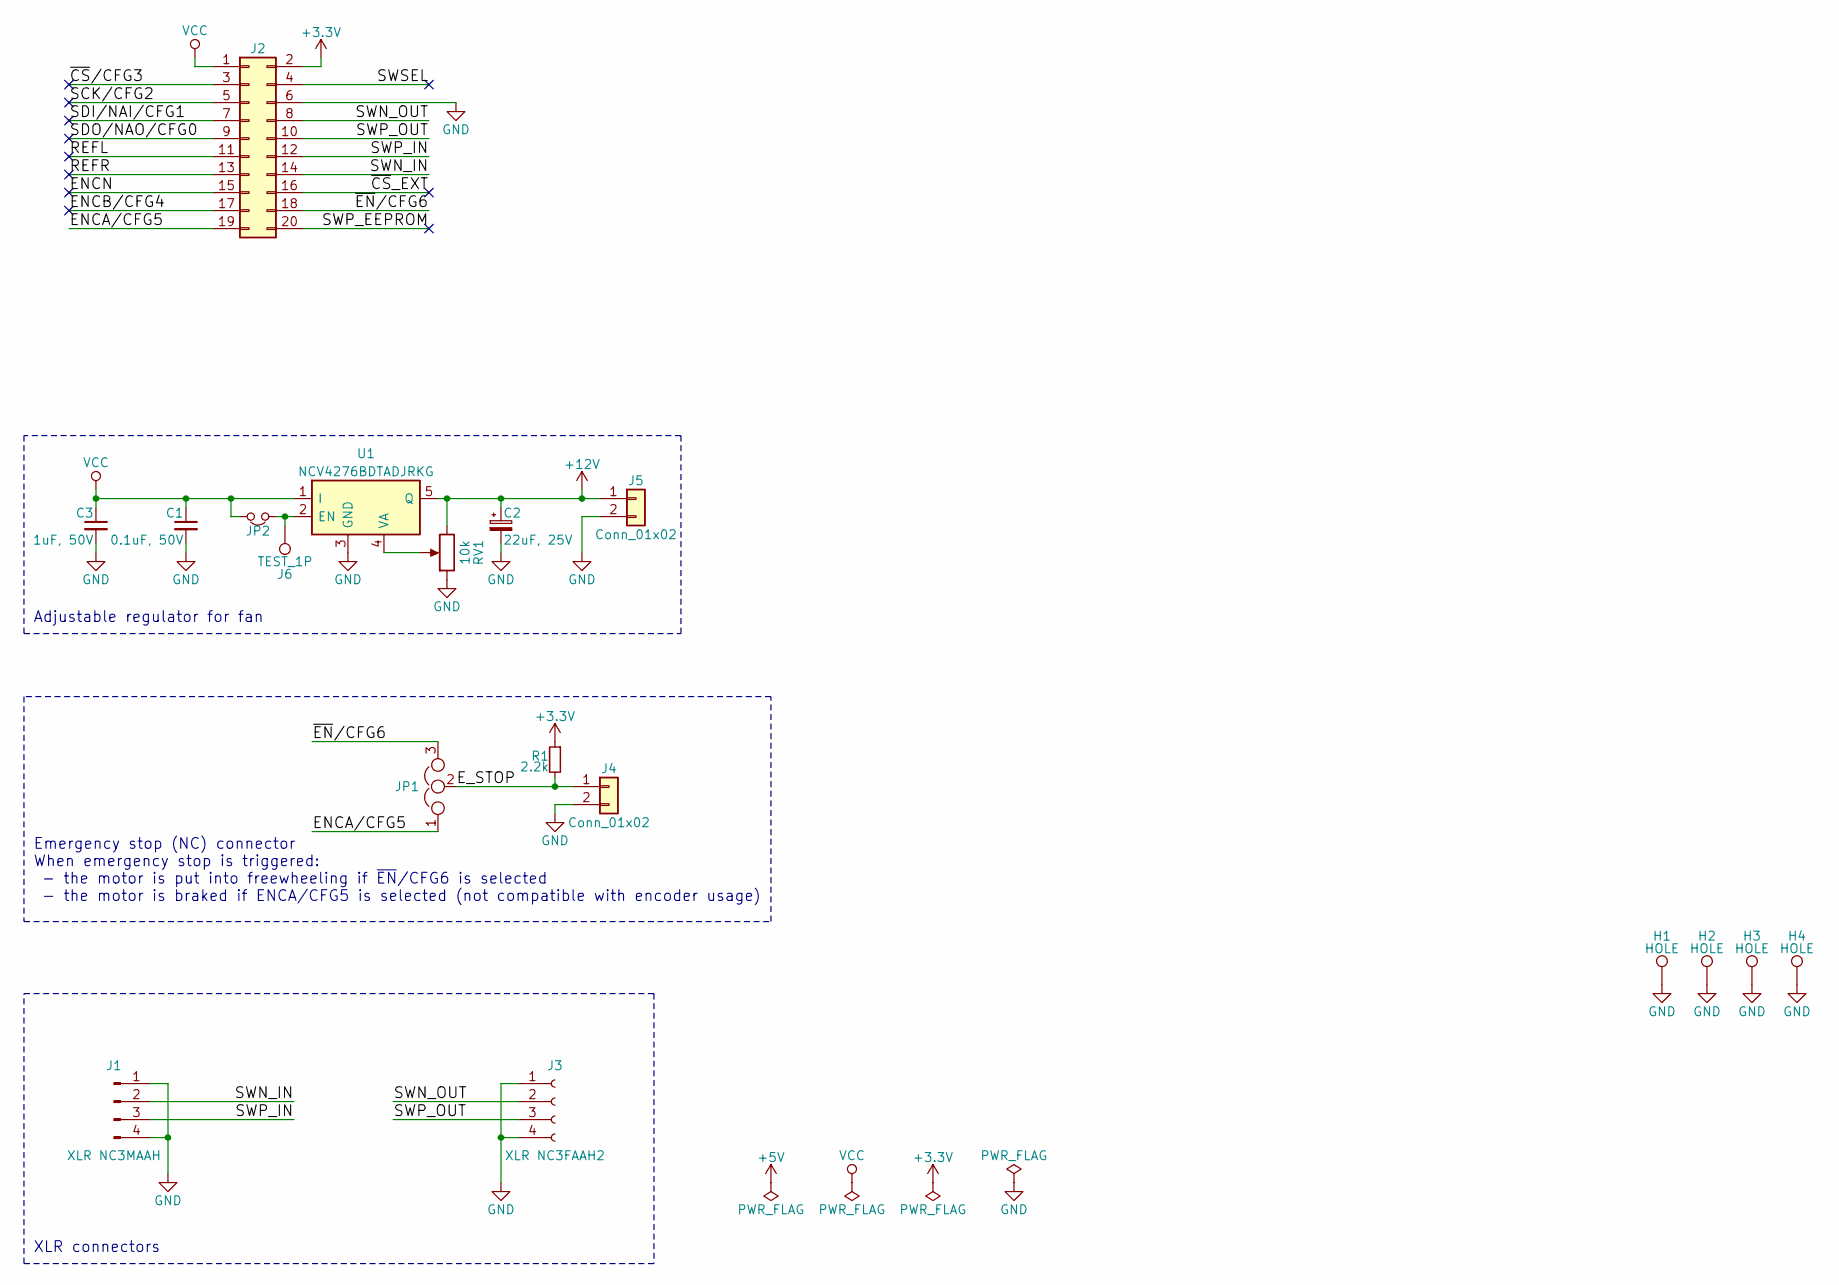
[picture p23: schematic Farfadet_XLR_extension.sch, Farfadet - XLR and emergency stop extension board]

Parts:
C1: 0.1uF, 50V; C_0603
C2: 22uF, 25V; CP_Elec_6.3x4.5
C3: 1uF, 50V; C_0805
H1, H2, H3, H4: HOLE; MountingHole_3.2mm_M3_Pad_Via
J1: XLR NC3MAAH; Neutrik_XLR_NC3MAAH
J2: Conn_02x10_Odd_Even; Socket_Strip_Straight_2x10_Pitch1.27mm_SMD
J3: XLR NC3FAAH2; Neutrik_XLR_NC3FAAH2
J4: Conn_01x02; TerminalBlock_Pheonix_MPT-2.54mm_2pol
J5: Conn_01x02; JST_PH_B2B-PH-K_02x2.00mm_Straight
J6: TEST_1P; PINTST
JP1: Jumper_NC_Dual; Solder_Jumper_3_open
JP2: Jumper_NC_Small; Solder_Jumper_2_conn
R1: 2.2k; R_0603
RV1: 10k; Potentiometer_Trimmer-EVM3E
U1: NCV4276BDTADJRKG; TO-252-4

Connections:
+3V3: J2.2, R1.1
+12V: C2.1, J5.1, RV1.3, U1.5 (Q)
/ENCA/CFG5: J2.19, JP1.1
/ENCB/CFG4: J2.17
/ENCN: J2.15
/E_STOP: J4.1, JP1.2, R1.2
/REFL: J2.11
/REFR: J2.13
/SCK/CFG2: J2.5
/SDI/NAI/CFG1: J2.7
/SDO/NAO/CFG0: J2.9
/SWN_IN: J1.2, J2.14
/SWN_OUT: J2.8, J3.2
/SWP_EEPROM: J2.20
/SWP_IN: J1.3, J2.12
/SWP_OUT: J2.10, J3.3
/SWSEL: J2.4
/~CS~/CFG3: J2.3
/~CS~_EXT: J2.16
/~EN~/CFG6: J2.18, JP1.3
GND: C1.2, C2.2, C3.2, H1.1, H2.1, H3.1, H4.1, J1.1, J1.4, J2.6, J3.1, J3.4, J4.2, J5.2, RV1.1, U1.3 (GND)
unnamed: J6.1, JP2.2, U1.2 (EN)
unnamed: RV1.2, U1.4 (VA)
VCC: C1.1, C3.1, J2.1, JP2.1, U1.1 (I)

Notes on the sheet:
XLR connectors
Emergency stop (NC) connector When emergency stop is triggered: - the motor is put into freewheeling if ~EN~/CFG6 is selected - the motor is braked if ENCA/CFG5 is selected (not compatible with encoder usage)
Adjustable regulator for fan

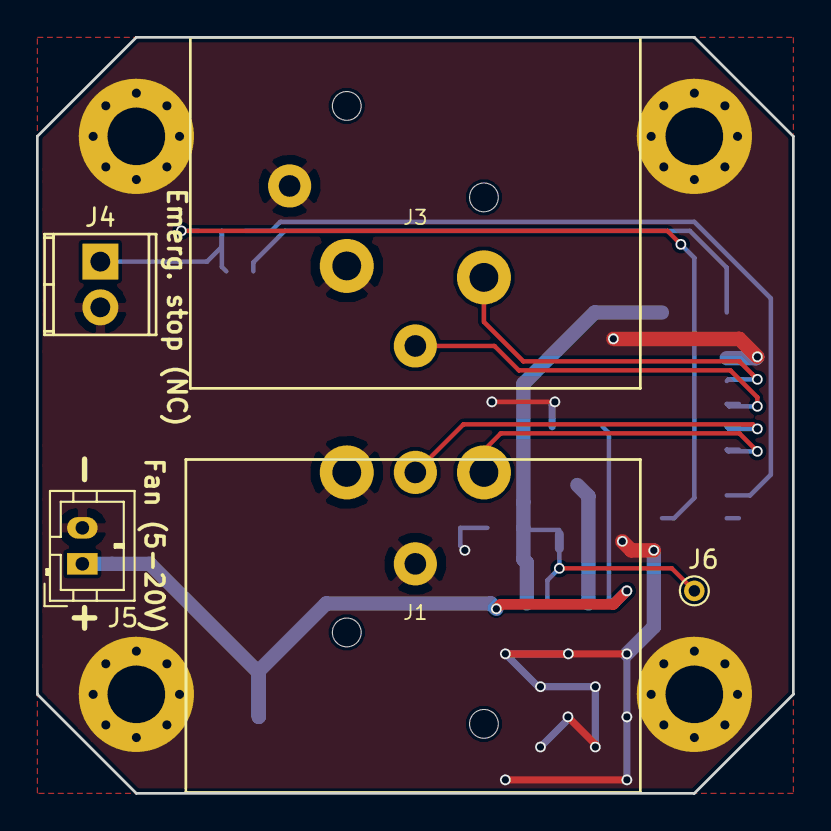
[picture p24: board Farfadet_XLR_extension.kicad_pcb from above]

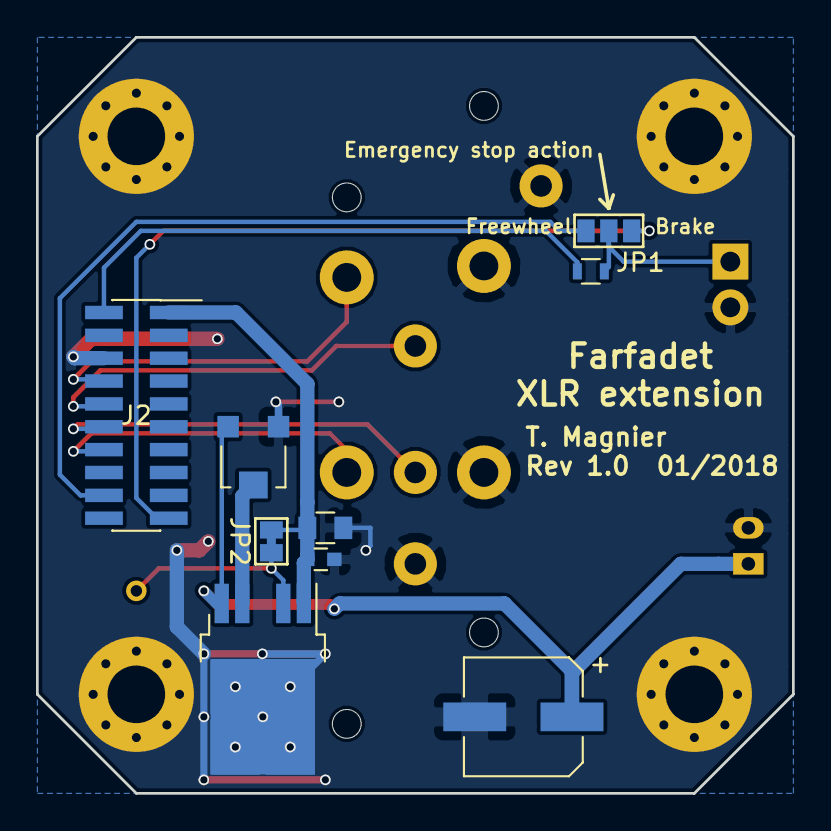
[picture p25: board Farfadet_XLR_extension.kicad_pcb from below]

Board: 2 copper layers, 42.0 x 42.0 mm, 18 parts (9 on the bottom side), 13 nets.

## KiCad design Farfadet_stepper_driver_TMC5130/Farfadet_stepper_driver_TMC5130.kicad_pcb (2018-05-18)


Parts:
C1: 220uF, 50V; CP_Elec_8x10.5
C2, C4, C5, C10, C15, C16: 0.1uF, 16V; C_0603
C3, C11, C14: 0.1uF, 50V; C_0603
C6: 10uF, 10V; C_0805
C7, C8: 4.7uF, 10V; C_0805
C9: 22nF, 63V; C_0603
C17, C22: DNP; C_0603
C18, C19, C20, C21: 470pF, 100V; C_0603
D1: 2A, 50V; D_SMA
D2, D3: D5V0L2B3W; SOT-323_SC-70
D6: Green; LED_0603
D7: Red; LED_0603
F1: 1.1A, 60V; Fuse_SMD2920
H1, H2, H3, H4: Mount_Hole; MountingHole_3.2mm_M3_Pad_Via
HS1: Heatsink; Heatsink_Adhesive_10x10mm
J1, J2, J11, J13: Conn_01x03; Molex_PicoBlade_53261-0371_03x1.25mm_Angled
J3: BARREL_JACK; JACK_ALIM
J5: Conn_02x10_Odd_Even; Pin_Header_Straight_2x10_Pitch1.27mm_SMD
J6: Conn_02x05_Odd_Even; Pin_Header_Straight_2x05_Pitch1.27mm_SMD
J7: TEST_1P; Measurement_Point_Round-TH_Small
J12: Conn_01x04; TerminalBlock_Pheonix_MPT-2.54mm_4pol
JP2: Jumper_NC_Small; Solder_Jumper_2_conn
JP3: Jumper_NO_Small; Solder_Jumper_2_open
R1, R6, R7, R9, R15, R18: 10k; R_0603
R2: 10R; R_0603
R3: 2.2k; R_0603
R4, R5: 0R12 0.5W; R_1206
R8, R10, R13, R16: 0R; R_0603
R11, R17: DNP; R_0603
R12, R14: 4.7k; R_0603
RV1: 10k; Potentiometer_Trimmer-EVM3E
U1: TS3A24159DGSR; TSSOP-10_3x3mm_Pitch0.5mm
U2: NCV4264-2ST50; SOT-223-3Lead_TabPin2
U3: MIC5365-3.3YD5; SOT-23-5
U4: DS2431P+T; TSOC-6_4x3.8mm_Pitch1.27mm
U5: TMC5130A; TQFP-48-1EP_7x7mm_Pitch0.5mm

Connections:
+3V3: C2.1, C4.1, C8.1, D6.2 (A), D7.2 (A), J5.2, J6.2, R3.1, R9.1, R10.1, R15.1, R16.1, R18.1, U1.1 (VCC), U3.5 (VOUT), U5.10 (VCC_IO)
+5V: C5.1, C6.1, J6.4, R1.1, R2.2, R11.1, R17.1, U2.3 (VO), U3.1 (VIN), U3.3 (EN), U5.34 (VCC), U5.39 (VSA)
/ENCA/CFG5: J5.19, J6.5, U5.25 (ENCA_DCIN_CFG5)
/ENCB/CFG4: J5.17, J6.3, U5.24 (ENCB_DCEN_CFG4)
/ENCN: J5.15, J6.1, R7.1, U5.23 (ENCN_DCO)
/REFL: C22.1, J5.11, R13.2, U5.8 (REFL_STEP)
/REFR: C17.1, J5.13, R8.2, U5.9 (REFR_DIR)
/SCK/CFG2: J5.5, J6.8, U5.4 (SCK_CFG2)
/SDI/NAI/CFG1: J5.7, J6.10, U5.5 (SDI_NAI_CFG1)
/SDO/NAO/CFG0: J5.9, J6.7, R14.2, U1.4 (IN1), U1.8 (IN2), U5.7 (SDO_NAO_CFG0)
/SD_MODE: JP2.1, U5.11 (SD_MODE)
/SPI_MODE: JP3.1, U5.12 (SPI_MODE)
/SWN_IN: D3.1 (A1), J1.2, J5.14, U1.9 (COM2), U5.26 (SWN_DIAG0)
/SWN_OUT: D2.1 (A1), J2.2, J5.8, U1.7 (NC2)
/SWP_EEPROM: J5.20, R3.2, U1.2 (NO1), U4.2 (IO)
/SWP_IN: D3.2 (A2), J1.3, J5.12, U1.3 (COM1), U5.27 (SWP_DIAG1)
/SWP_OUT: D2.2 (A2), J2.3, J5.10, U1.5 (NC1)
/SWSEL: J5.4, R18.2, U5.28 (SWSEL)
/~CS~/CFG3: J5.3, U5.3 (CSN_CFG3)
/~CS~_EXT: J5.16, J6.6
/~EN~/CFG6: J5.18, R6.1, U5.29 (DRV_ENN_CFG6)
GND: C1.2, C2.2, C3.2, C4.2, C5.2, C6.2, C7.2, C8.2, C11.2, C14.2, C15.2, C16.2, C17.2, C18.2, C19.2, C20.2, C21.2, C22.2, D1.2 (A), D2.3 (common), D3.3 (common), H1.1, H2.1, H3.1, H4.1, HS1.1, J1.1, J2.1, J3.2, J3.3, J5.6, J6.9, J11.3, J13.3, JP2.2, JP3.2, R4.2, R5.2, R6.2, R7.2, R12.2, RV1.3, U1.6 (GND), U1.11 (PAD), U2.2 (GND), U3.2 (GND), U4.1 (GND), U5.1 (TST_MODE), U5.2 (CLK), U5.6 (NC), U5.13 (GNDP), U5.31 (NC), U5.32 (GNDA), U5.36 (NC), U5.48 (GNDP), U5.49 (GNDD)
unnamed: C7.1, R2.1, U5.33 (5VOUT)
unnamed: C9.1, U5.35 (CPO)
unnamed: C9.2, U5.37 (CPI)
unnamed: C10.2, U5.38 (VCP)
unnamed: C15.1, R4.1, U5.44 (BRA)
unnamed: C16.1, R5.1, U5.17 (BRB)
unnamed: C18.1, J12.2, U5.42 (OA2)
unnamed: C19.1, J12.3, U5.19 (OB2)
unnamed: C20.1, J12.1, U5.46 (OA1)
unnamed: C21.1, J12.4, U5.15 (OB1)
unnamed: D6.1 (K), R12.1
unnamed: D7.1 (K), R14.1
unnamed: F1.2, J3.1
unnamed: J7.1, RV1.2, U5.30 (AIN_IREF)
unnamed: J11.1, R10.2, R11.2
unnamed: J11.2, R8.1, R9.2
unnamed: J13.1, R16.2, R17.2
unnamed: J13.2, R13.1, R15.2
unnamed: R1.2, RV1.1
VCC: C1.1, C3.1, C10.1, C11.1, C14.1, D1.1 (K), F1.1, J5.1, U2.1 (VI), U5.21 (VS), U5.40 (VS)

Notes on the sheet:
Stepper motor
DC IN 5 - 45V
RS485-like data IN
RS485-like data OUT
5V, 100mA regulator
3.3V, 150mA regulator
Bus switch : on reset NAO is HIGH. The 1-Wire EEPROM is connected to the serial bus. After configuration NAO is set to LOW. The EEPROM is disconnected and the next device on the bus gets connected.
Power management
On-board EEPROM and serial number
Power & Config OK LEDs
Optional limit switches with RC filter Mechanical, optical or hall-effect switches can be used.
SD_MODE low : internal ramp generator SPI_MODE high : serial/SPI control
Optional encoder connector
SWSEL high : single wire interface
Special configuration jumpers

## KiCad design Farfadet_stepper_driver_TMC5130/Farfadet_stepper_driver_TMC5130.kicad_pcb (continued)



Board: 4 copper layers, 42.0 x 42.0 mm, 72 parts (58 on the bottom side), 42 nets.

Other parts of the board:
FID1, FID2, FID3, FID4, FID5, FID6: Fiducial_very_small_modern

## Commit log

2018-05-18 Add hardware files for the following PCBs : * TMC5130 stepper motor driver v1.1 * Magnetic encoder extension v1.0 * XLR connector extension v1.0 * Minimal 5V / 3.3V differential transceiver v1.0
    [Farfadet_XLR_extension-B.Cu.gbl, Farfadet_XLR_extension-B.Mask.gbs, Farfadet_XLR_extension-B.Paste.gbp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]
2018-06-13 Differential transceiver : fix XLR connector pinout
    [Farfadet_differential_transceiver-B.Cu.gbl, Farfadet_differential_transceiver-B.Mask.gbs, Farfadet_differential_transceiver-B.Paste.gbp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]
2018-06-13 Magnetic encoder extension v1.1 : add resistive voltage dividers on 5V signals
    [Farfadet_magnetic_encoder_extension-B.Cu.gbl, Farfadet_magnetic_encoder_extension-B.Mask.gbs, Farfadet_magnetic_encoder_extension-B.Paste.gbp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]
2018-06-13 Add Farfadet dual transceiver FeatherWing v1.0
    [Farfadet_dual_transceiver_featherwing-B.Cu.gbr, Farfadet_dual_transceiver_featherwing-B.Mask.gbr, Farfadet_dual_transceiver_featherwing-B.Paste.gbr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]
2018-06-13 Add Gerber archives
2018-06-13 Add KiCad cache lib files to all designs
2018-06-13 Update Magnetic encoder extension BOM
    [Farfadet_magnetic_encoder_extension_BOM.ods]
2018-06-20 Update magnetic encoder extension v1.1 fab drawing
